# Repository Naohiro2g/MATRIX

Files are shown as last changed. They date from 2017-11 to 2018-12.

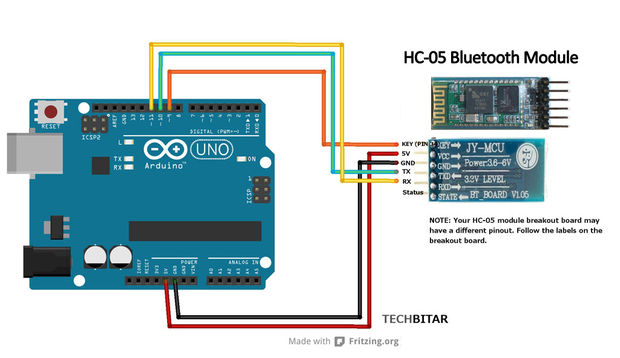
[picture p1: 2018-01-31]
Test/Setup/HC05_BT_config/HC05_BT_config_connect.jpg

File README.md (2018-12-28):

# Otto LED Matrix for mouth emotions

LED mouth Matrix use the [MAX7219](https://es.aliexpress.com/item/1pcs-MAX7219-dot-matrix-module-microcontroller-module-display-module-finished-goods/32725083862.html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)
+Touch sensor use this [2PCS TTP223 Capacitive Touch Switch Button Self-Lock Module for Arduino](http://www.ebay.com/itm/2PCS-TTP223-Capacitive-Touch-Switch-Button-Self-Lock-Module-for-Arduino/131662428748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)

Here are libraries and sketches for Otto DIY robot, with all files neccesary for LED Matrix and some features under developmnet

- Bluetooth
- rechargable lipo battery
- touch sensors
- RGB led nose
- LED matrix for mouths
- internal voltage measurment

v2 sketch is for version with 2 buttons for mode change (first button dance, second button walk+avoid, both together = react to noise)
v3 sketch has only 1 button or touch sensor and changes modes on touch (dance -> walk -> react to noise -> standby -> dance....)
Everything else is the same.

## 1. Interact with other Otto builders
Join the [Otto builders group in facebook](https://www.facebook.com/groups/ottodiy/)

## 2. Buy to build or make your own Otto!
Difficult to find all the parts? then buy quality kits [from our website only](ottodiy.com), is a way to contribute and support this project to continue growing, so we can continue offering very affordable kits and constantly creating new robots open for all.
After you have all components just follow the instruction manual in the files and build your own Otto in one hour!

If you want make Otto by yourself ;) that is great too! but do not forget to add your [marker in our google map!](https://drive.google.com/open?id=1qXEfuS5egbF14gi8EUjJ6U-dITHoJJNZ&usp=sharing)

## 3. Share your innovative creation with #OttoDIY
A redesign, modified code or if your creation is different but inspired in Otto; is technically a remix, so please share in our [Wikifactory Social & Design Platform](https://wikifactory.com/+OttoDIY) or please post that you have [made/remix an Otto in Thingiverse and add to this group] (https://www.thingiverse.com/groups/ottodiy) or pull a request here in Github!

Keep sharing with us in any social media, tag friends, family with #OttoDIY and make sure more robot fans do the same everywhere, we love to see Otto robots around the world!

Please help us to spread out the word first in Maker Faires, Maker spaces, Hacker spaces, Schools, Universities, tech events and so on...

## 4. Otto DIY robot for STEAM education 
Educational deep content for STEAM centers, we already partner with many tech companies, entrepreneurs, educational centers and schools around the world, just contact us to be an official collaborator, we easily adapt to different curriculum or needs and we can leverage your ideas too!
Add your [organization in our google map](https://drive.google.com/open?id=1qXEfuS5egbF14gi8EUjJ6U-dITHoJJNZ&usp=sharing) and do not hesitate to contact us

Stay active in our social media for contest and awards to the best Otto builders and as always so we will keep sharing this knowledge to the world and the humanity.

Truly opensource hardware!

## License CC-BY-SA
<br /><span xmlns:dct="http://purl.org/dc/terms/" property="dct:title">Otto DIY</span> by <a xmlns:cc="http://creativecommons.org/ns#"  property="cc:attributionName"> [www.ottodiy.com](http://www.ottodiy.com) </a> is licensed under a <a rel="license" href="http://creativecommons.org/licenses/by-sa/4.0/">Creative Commons Attribution-ShareAlike 4.0 International License</a>.

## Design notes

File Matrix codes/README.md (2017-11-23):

# LED Matrix (optional)

This Repository have all open source files for @jarsoftelectrical version of the popular Otto DIY 
The Arduino code is modified from the Zowi robot, it has modified to wotk with a MAX 7219 LED MATRIX as as mouth as well as other adjustments.

Please copy all the files in the OTTO_Library folder to the Arduino IDE Library folder
The code is based on the Zowi code, modified for OTTO
Please NOTE: i have moved the BUZZER to pin D13............
Please NOTE: you need pull-down resistors on the button pins............
Please NOTE: you will need a link between A7 and +5 volt to fool low battery warnings

OTTO main program is  inside the OTTO_LEDMATRIX folder, ensure you are using the latest version of the Arduino IDE.
The modifed ZOWI main program is inside the ZOWI_BASE_v2_MATRIX folder, ensure you are using the latest version of the Arduino IDE.

Happy roboting....

Otto was inspired by another robot BoB the BiPed and programmed using code from [another open source biped robot Zowi](https://github.com/bqlabs/zowi)

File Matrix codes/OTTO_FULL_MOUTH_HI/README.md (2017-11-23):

# Otto DIY PLUS

This Repository have all open source files for my version of the popular Otto DIY PLUS with the OTTO welcome on 7219MAX MATRIX LED mouth
The Arduino code is modified from the Zowi robot and original OTTO code, it has modified to work with a MAX 7219 LED MATRIX as as mouth as well as other software adjustments.

Please copy all the files in the Library folder to the Arduino IDE Library folder

The main program is inside the OTTO_FULL_MOUTH_HI folder, ensure you are using the latest version of the Arduino IDE.

Happy roboting....

Otto was inspired by another robot BoB the BiPed and programmed using code from [another open source biped robot Zowi](https://github.com/bqlabs/zowi)

## License CC-BY-SA
<br /><span xmlns:dct="http://purl.org/dc/terms/" property="dct:title">OttoDIY</span> by <a xmlns:cc="http://creativecommons.org/ns#" href="ottobot.org" property="cc:attributionName" rel="cc:attributionURL">ottobot.org</a> is licensed under a <a rel="license" href="http://creativecommons.org/licenses/by-sa/4.0/">Creative Commons Attribution-ShareAlike 4.0 International License</a>.

Otto's differences are in the assembled size (11cm x 7cm x12cm), cleaner integration of components and expressions. 
Using off the shelf and 3D printed parts, simple electronics connections (almost no welding required), and basic coding skills, [you will be able to build your own cute Otto friend in as little as two hours!](http://www.instructables.com/id/Otto-Build-You-Own-Robot-in-Two-Hours/)

### Otto is design using Autodesk 123D Design software 
[You can modify it for customization](http://www.123dapp.com/Project/Otto-build-your-own-robot/5658683) or further improvements!
Gather all the off the shelf parts in the [BOM file] (https://github.com/OttoDIY/Otto/blob/master/OTTO_V02_BOM_STP_STL/OTTO_BOM.xlsx) that you'll need for this assembly, then follow [the instruction manual] (https://github.com/OttoDIY/Otto/blob/master/OTTO_V02_BOM_STP_STL/OTTO_InstructionManual_V02.pdf)

This robot is licensed under a Creative Commons Attribution-ShareAlike 4.0 International License. Please read the LICENSE files for more details.

More info in http://ottobot.org

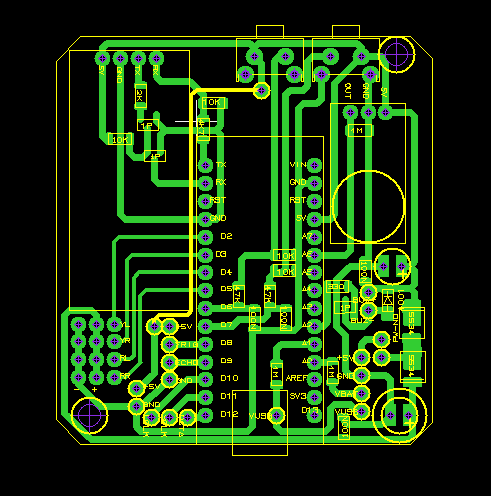
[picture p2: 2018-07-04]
PedroBot_Main_Prog/Implantation Main Board.PNG

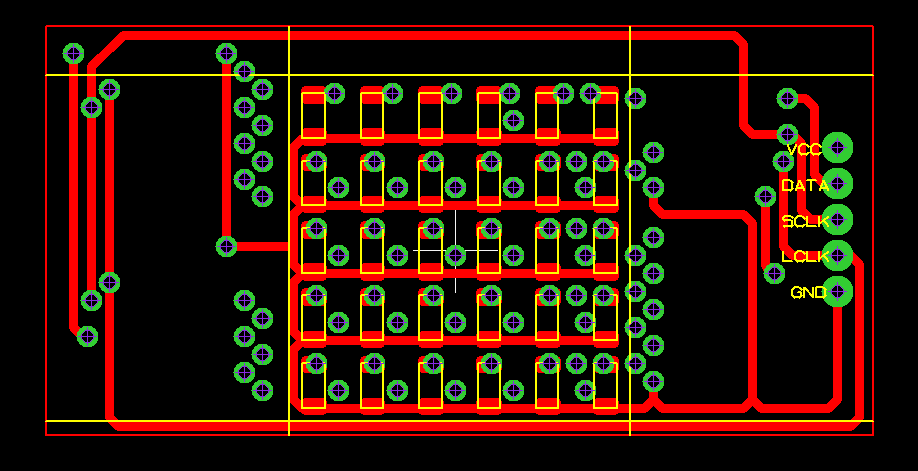
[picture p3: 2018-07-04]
PedroBot_Main_Prog/Matrix led back layer.PNG

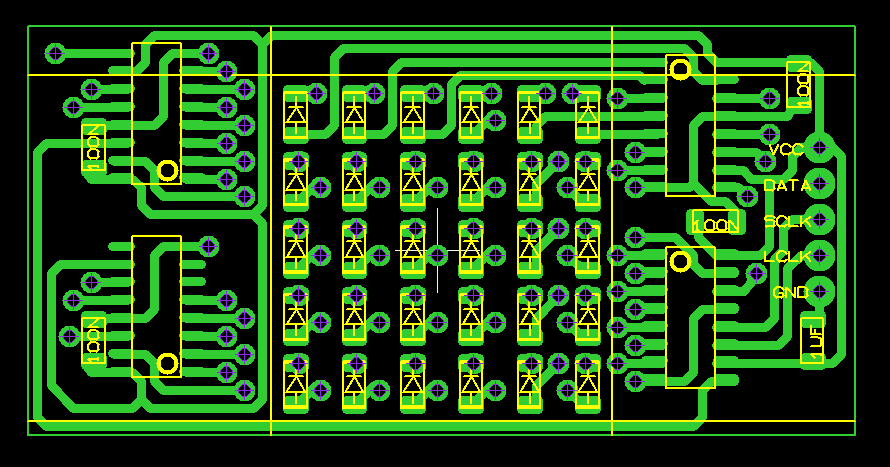
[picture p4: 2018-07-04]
PedroBot_Main_Prog/Matrix led front layer.PNG

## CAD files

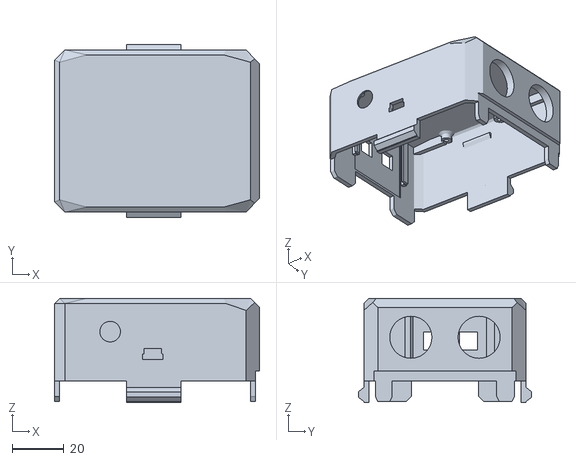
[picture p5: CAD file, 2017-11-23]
CAD/Head_MATRIX_5.stl
79.5 x 67.2 x 40.4

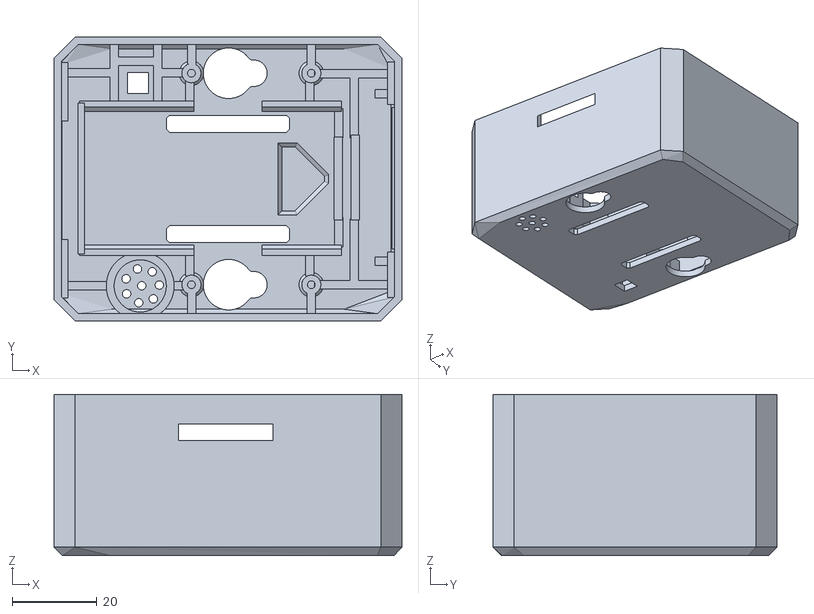
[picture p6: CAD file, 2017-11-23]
CAD/Body_MATRIX_4.stl
82.0 x 67.0 x 38.0

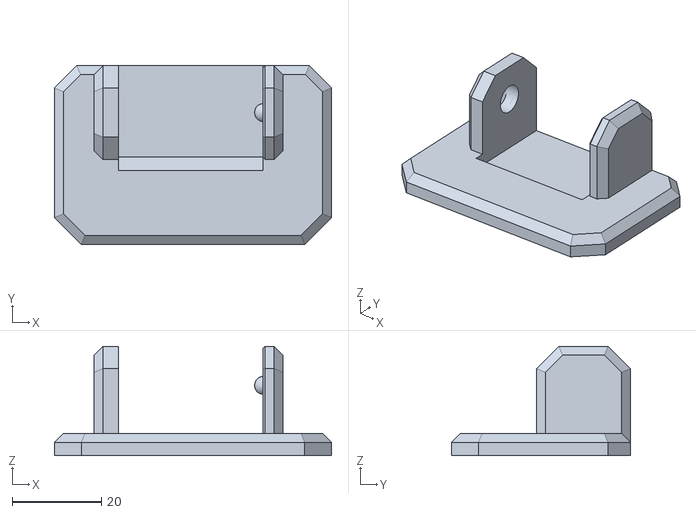
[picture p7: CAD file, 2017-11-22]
CAD/Pied droit v2.1 MG.stl
62.0 x 40.0 x 24.5

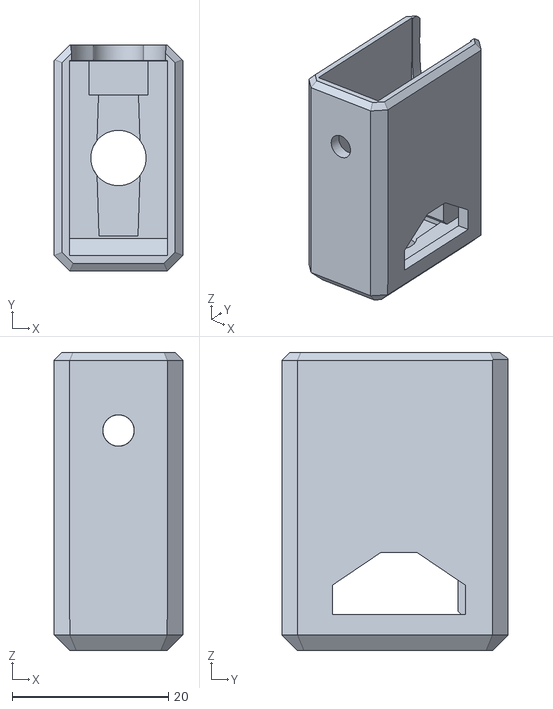
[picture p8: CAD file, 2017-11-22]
CAD/Jambes v2.0.stl
16.5 x 29.0 x 38.2

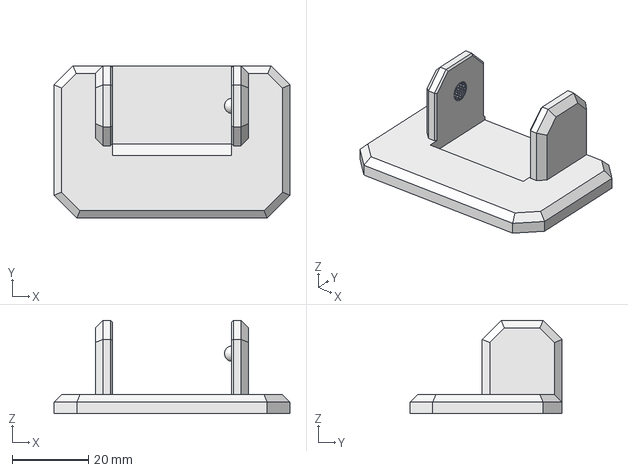
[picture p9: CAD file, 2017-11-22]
CAD/Pied droit.FCStd
62.0 x 40.0 x 24.5 mm

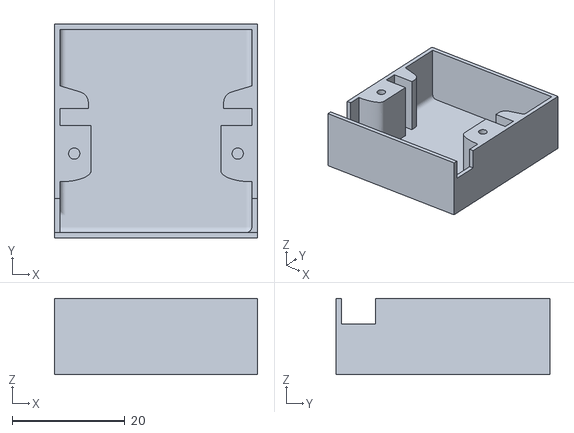
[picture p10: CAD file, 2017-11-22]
CAD/TowerPro_MG90_servo_box.STL
36.0 x 38.0 x 13.5

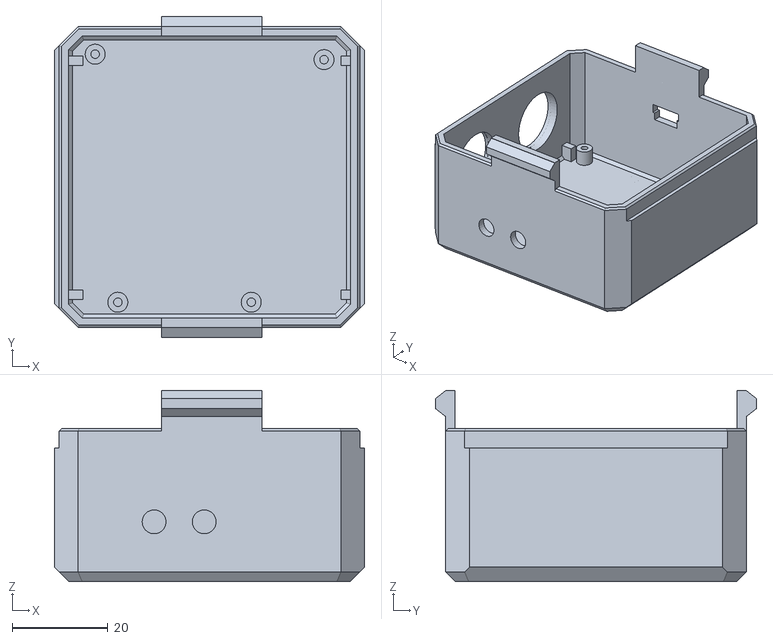
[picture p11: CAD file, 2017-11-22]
CAD/Tete v1.3.stl
65.0 x 67.2 x 40.0

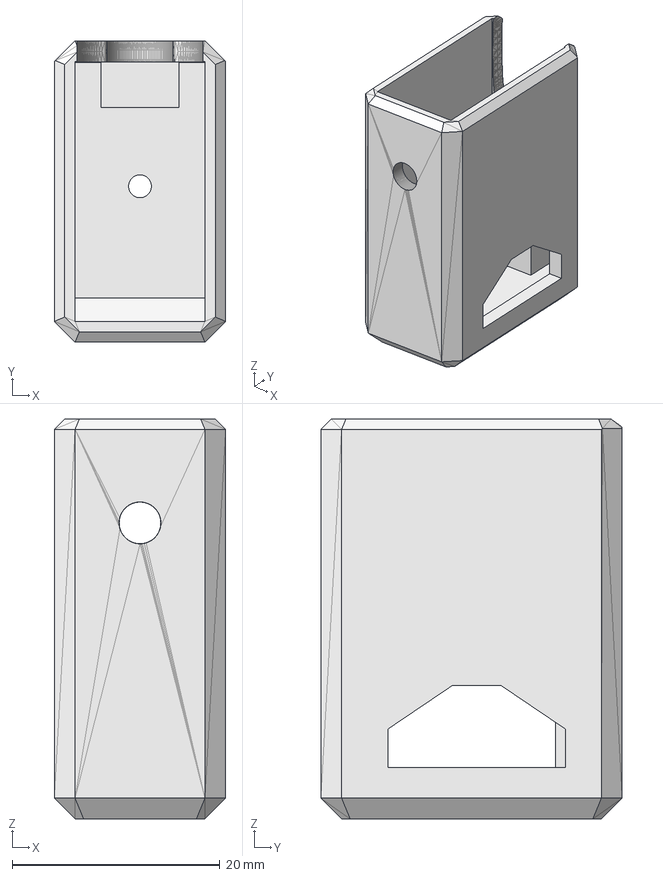
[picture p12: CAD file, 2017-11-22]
CAD/Jambes.FCStd
16.5 x 29.0 x 38.5 mm

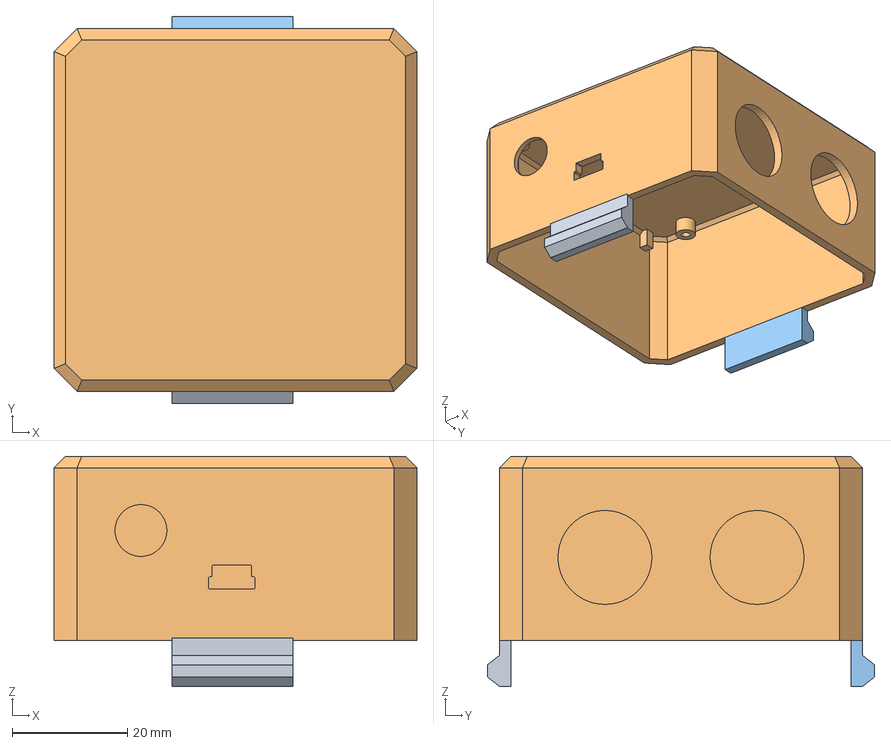
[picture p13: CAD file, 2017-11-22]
CAD/Tete.FCStd
63.0 x 67.2 x 40.0 mm
OTTO_snap037
OTTO_snap035
OTTO_snap036

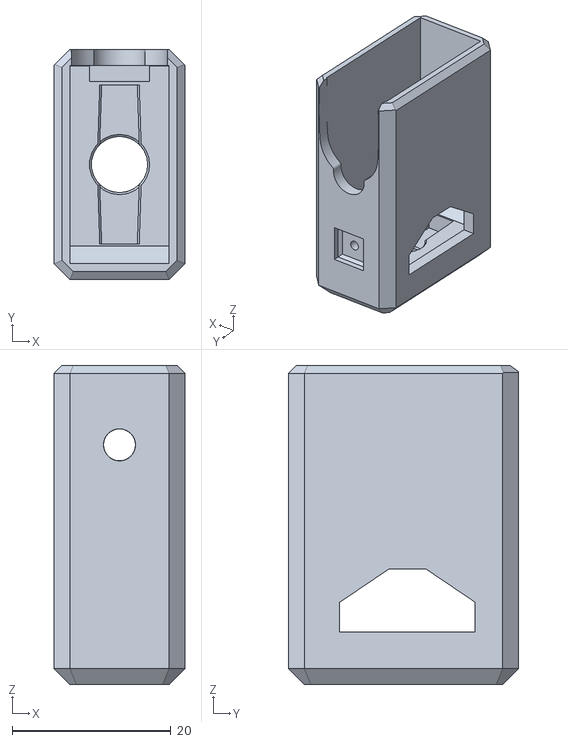
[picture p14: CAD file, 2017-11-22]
CAD/Jambes v2.2 MG.stl
16.5 x 29.0 x 40.2

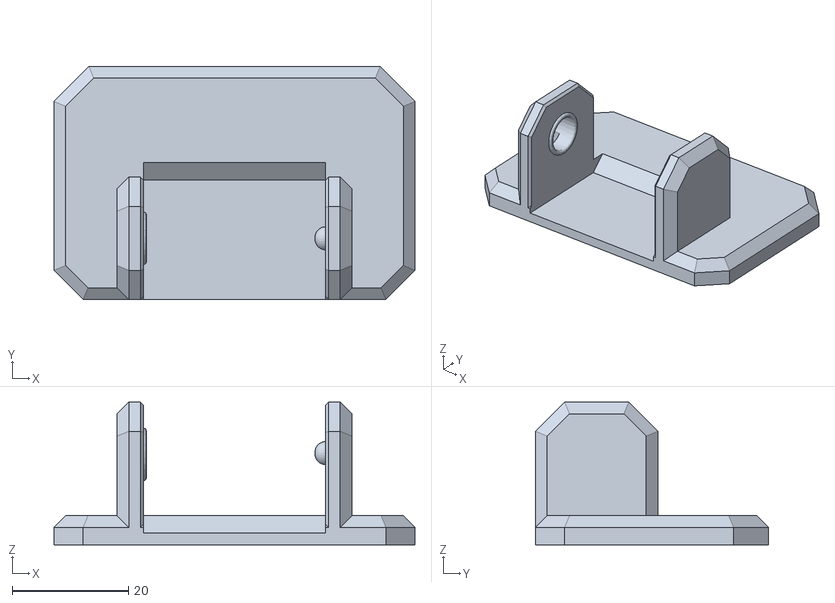
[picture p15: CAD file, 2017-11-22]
CAD/Pied gauche v2.0.stl
62.0 x 40.0 x 24.5

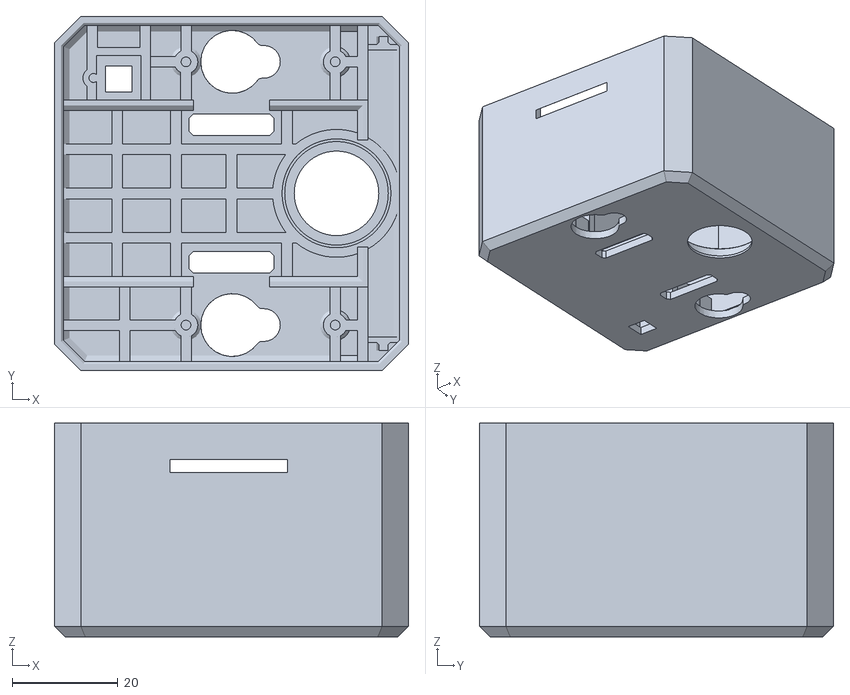
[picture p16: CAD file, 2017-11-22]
CAD/Corps v1.5 MG.stl
67.0 x 67.0 x 40.5

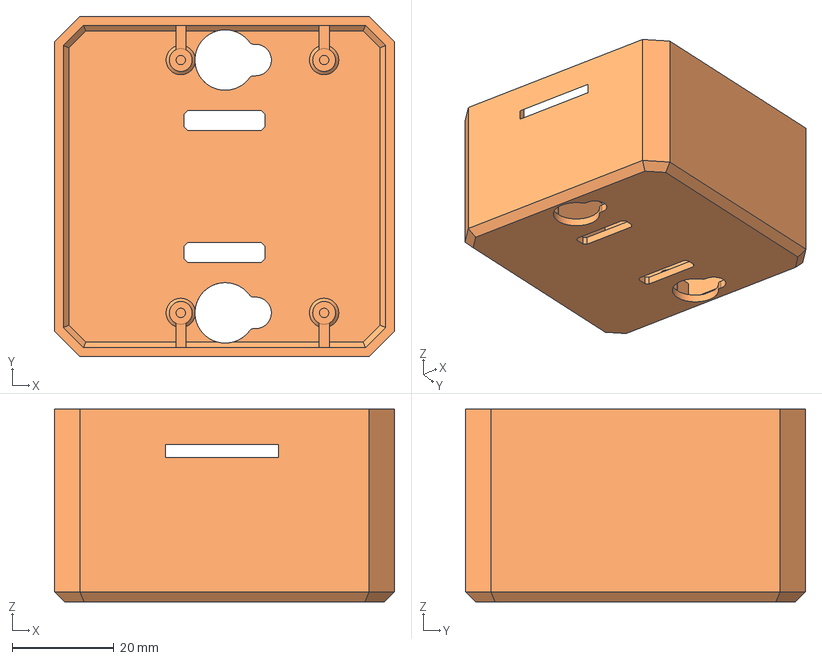
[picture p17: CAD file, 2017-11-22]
CAD/Corps.FCStd
67.0 x 67.0 x 38.0 mm

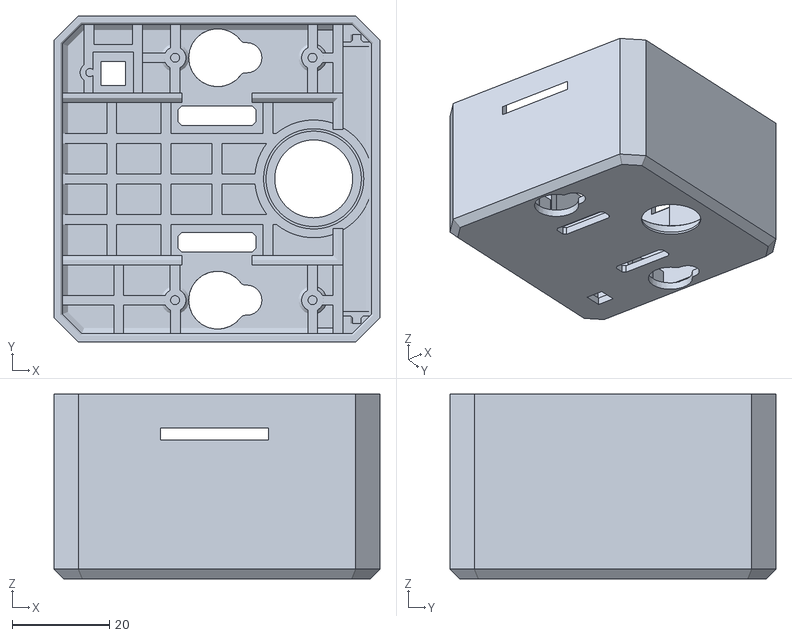
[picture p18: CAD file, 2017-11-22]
CAD/Corps v1.4.stl
67.0 x 67.0 x 38.0

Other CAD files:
CAD/Pied droit v2.0.stl
CAD/Pied gauche.FCStd
CAD/Pied gauche v2.1 MG.stl

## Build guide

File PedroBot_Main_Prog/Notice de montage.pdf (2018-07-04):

Montage de PedroBot
Auteur | Message
Pedro-51 | Sujet: Montage de PedroBot Lun 22 Mai 2017 - 1:23
| Il s'agit là d'un document que j'ai écris pour aider les enfants de mon club technologie à construire leurs robot.
| Il est bien évident que dans un cadre éducatif, il faudra fabriquer les cartes électroniques et préparer les différents éléments pour en arriver à un kit accessible aux enfants. Mais également pour celle et ceux qui souhaitent créer leurs propres robots à titre personnel, je vous invite à lire mes autres posts qui détail la marche à suivre pour fabriquer ces différents éléments.

# Montage de PedroBot

| Fabriquer un robot entièrement reprogrammable qui ce déplace tout seul, pouvant éviter des obstacles, réagir au son, danser et plus encore? Tout cela à la porté des enfants... grâce au projet PedroBot, c'est possible.
| PedroBot, qu'est ce que c'est? Il s'agit en fait de l'évolution d'un projet open source s'appelant «Otto bot» diffusé sur internet afin de faciliter l'apprentissage de la programmation aux enfants.
| Le robot que je propose et en fait une version de ma propre conception similaire à un modèle provenant d'une société Espagnol appelé BQ, qui se sont eux même inspiré du projet d'origine pour développer leur propre produit vendu en France à 129,90€ sur leurs site internet.

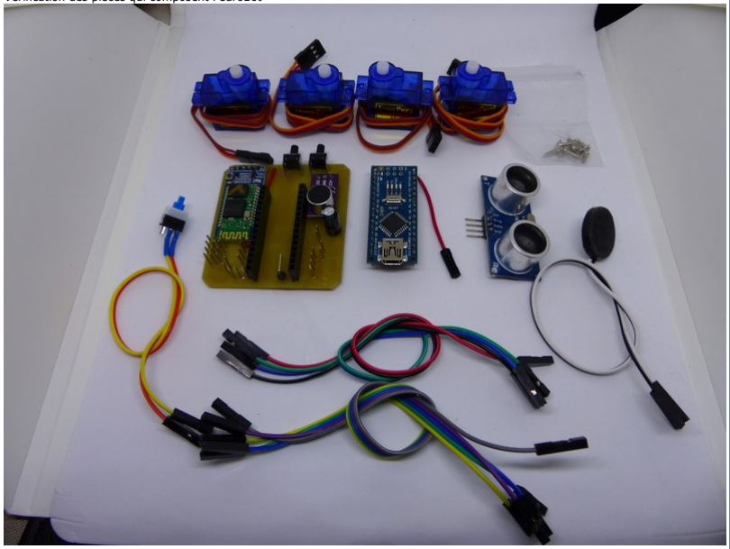
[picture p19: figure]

| Vérification des pièces qui composent PedroBot

Insére le servo-moteur dans le corps de PedroBot puis visse ce dernier.

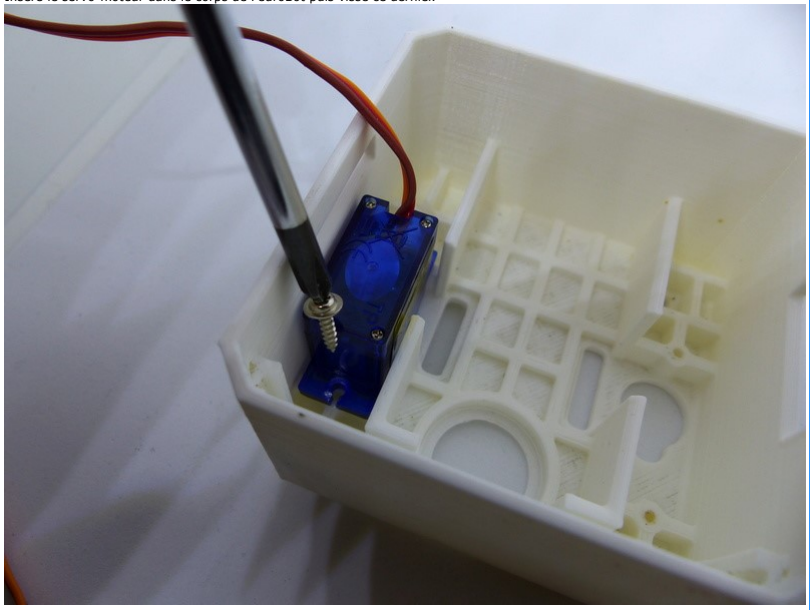
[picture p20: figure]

Fait de même pour le second servo-moteur.

Monte les jambes exactement comme sur la photo. Veille à ne pas tourner les servos-moteurs manuellement. Ils ont préalablement été réglés pour faciliter le montage.

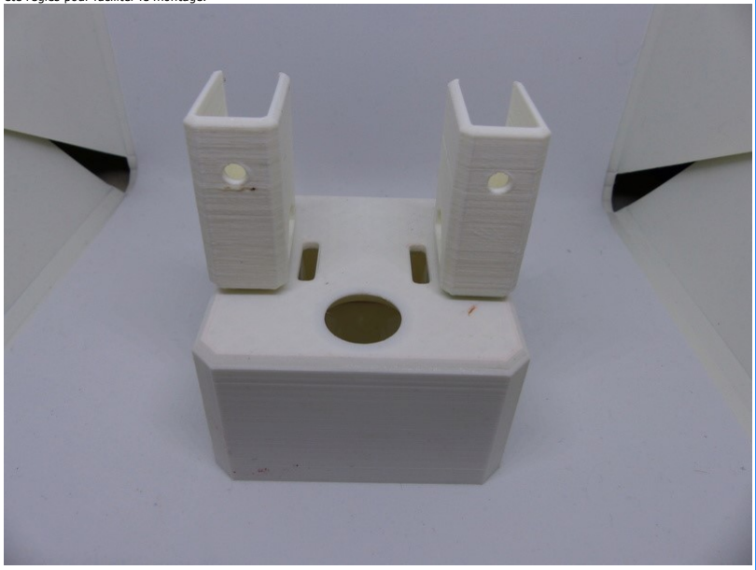
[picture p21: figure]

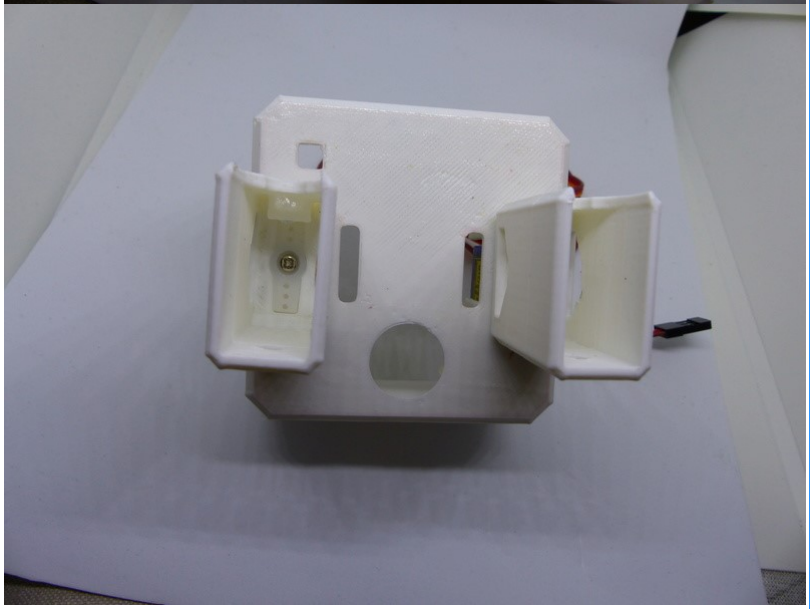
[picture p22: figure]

Insére les servos-moteurs. Comme pour les jambes, ne tourne pas les servos-moteurs manuellement.

Visse les servos-moteurs

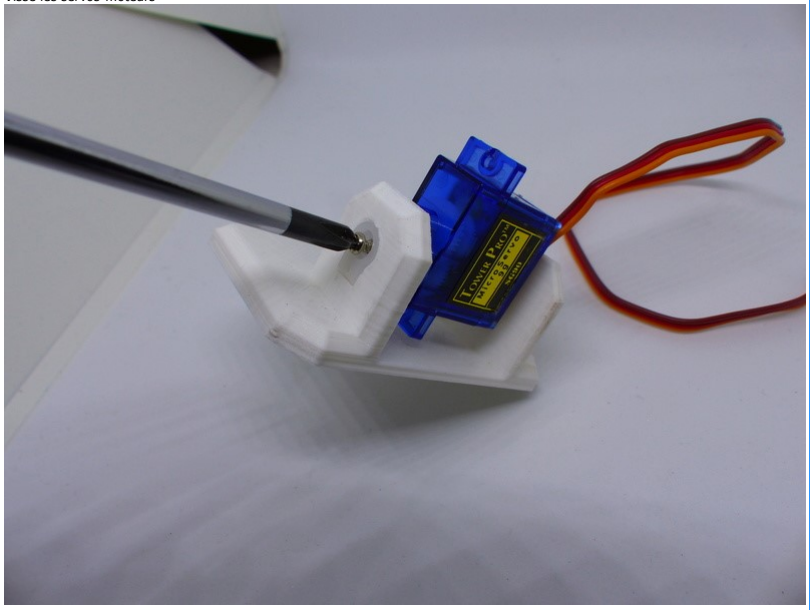
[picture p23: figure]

Place les câbles des pieds comme indiqué sur la photo.

Insére les servos-moteurs dans les jambes.

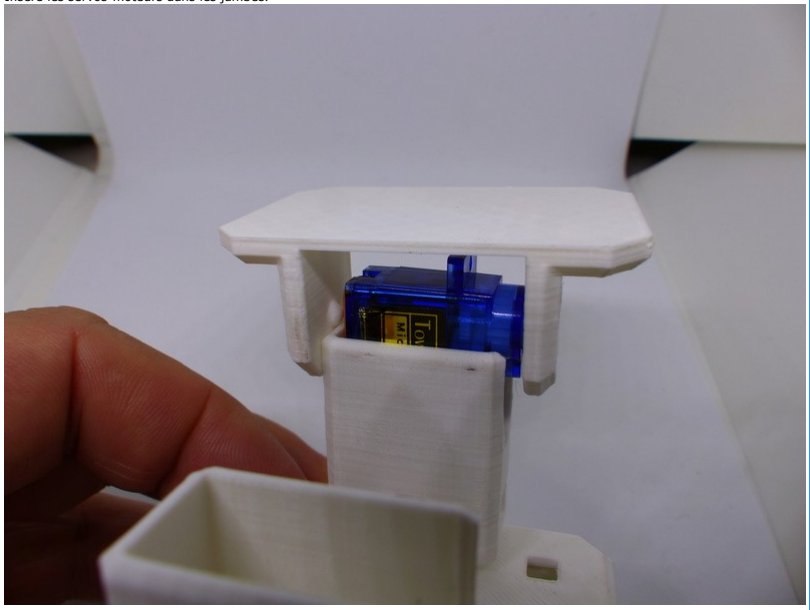
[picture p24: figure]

Visse les servos-moteurs.

Place le Haut parleur dans le corps du robot

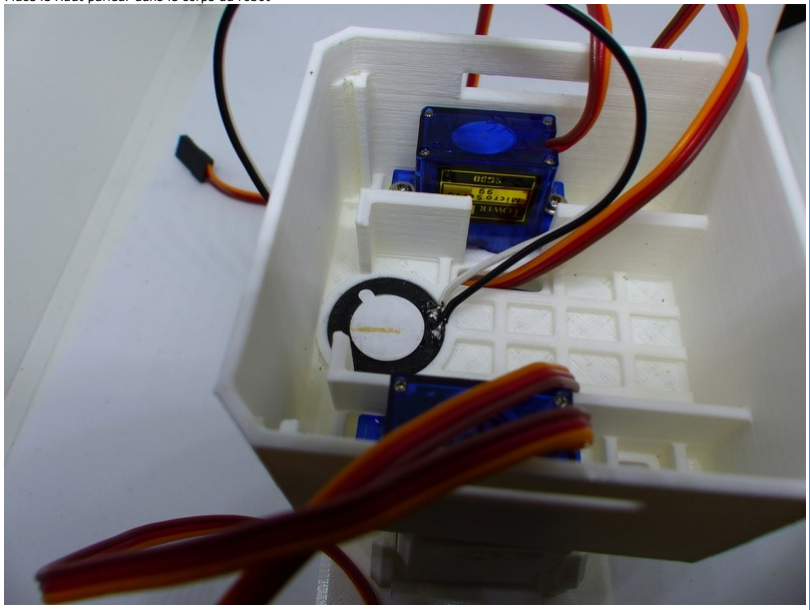
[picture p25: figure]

Fait de même pour l'interrupteur, bloque celui ci à l'aide d'une longue vis.

Prend la carte Arduino Nano et branche le câble qui permettra la charge de la batterie.

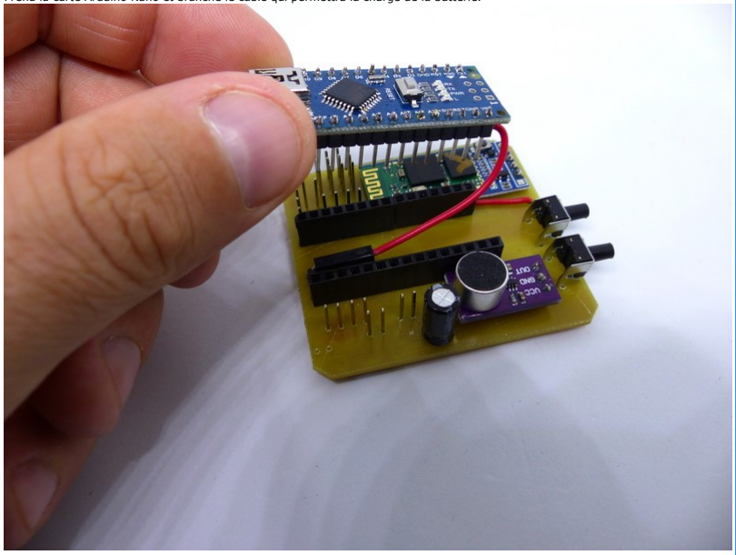
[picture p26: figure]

Insére la carte Arduino à la carte principale.

Branche les fils qui serviront à connecter le Capteur Ultrason.

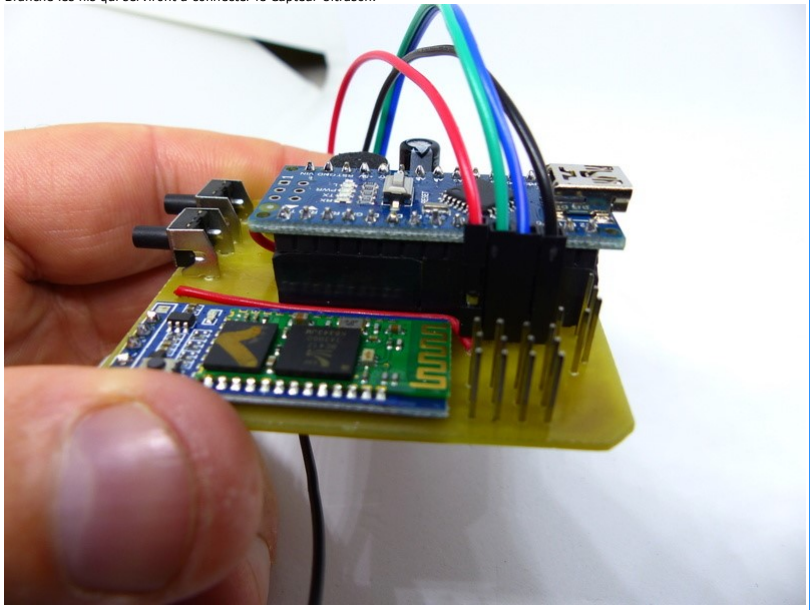
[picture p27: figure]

Branche les câbles du haut parleur et de l’interrupteur. Respecte le code couleur.

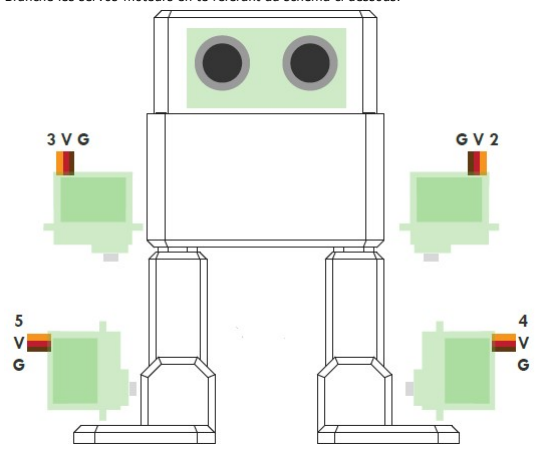
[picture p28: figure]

Branche les servos-moteurs en te référant au schéma ci dessous.

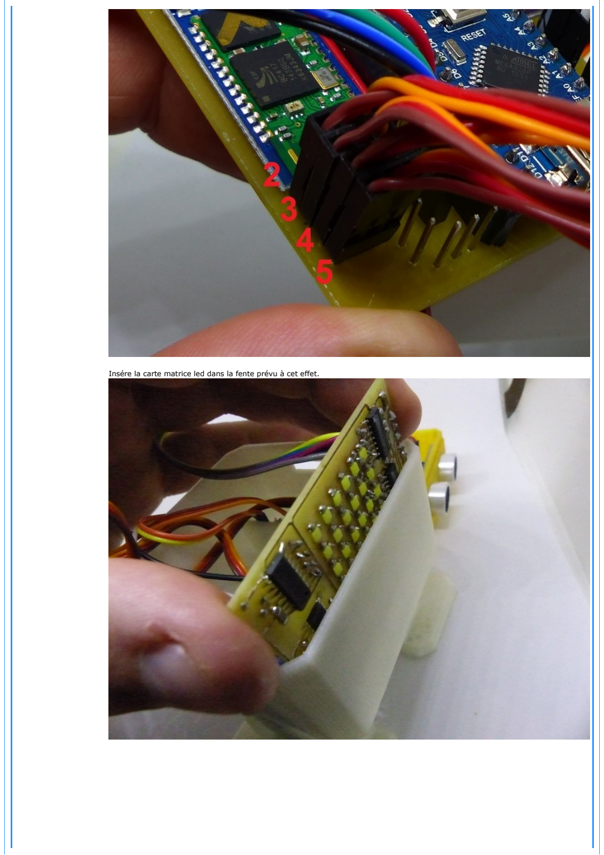
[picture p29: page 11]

Insére la carte matrice led dans la fente prévu à cet effet.

Branche la carte matrice led.

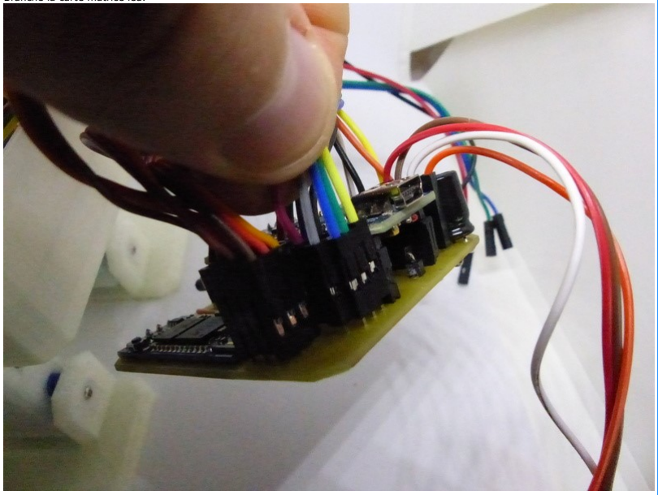
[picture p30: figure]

Branche le pack batterie

Insére le Pack batterie dans sont logement.

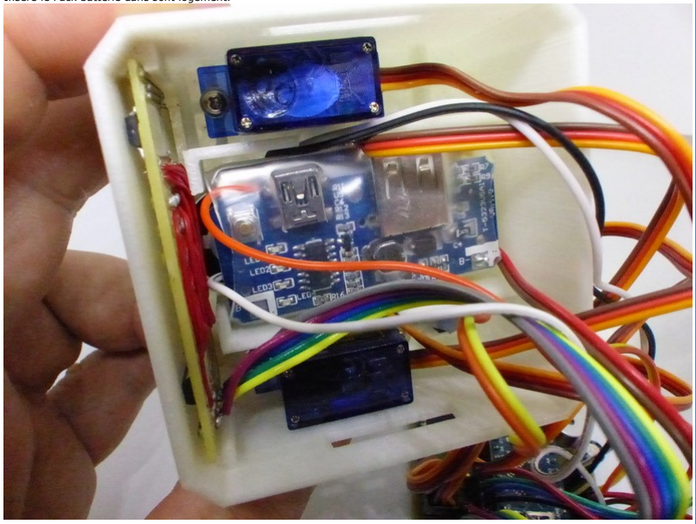
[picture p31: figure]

Insére le capteur à Ultra Son dans la tête de PedroBot.

Rentre la carte principal en diagonale en veillant a ce que les interrupteurs soit placés correctement dans leurs logements.

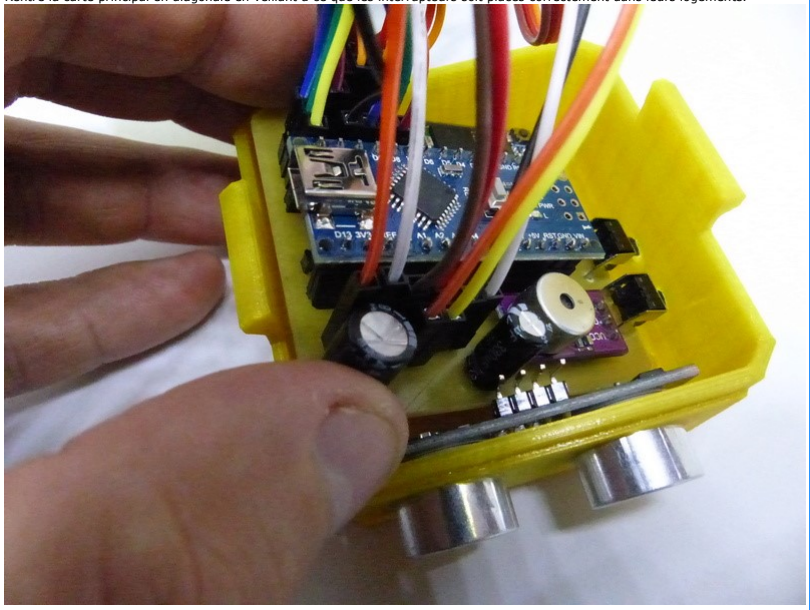
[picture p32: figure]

Enfonce la carte au fond de la tête, un clic se fera entendre lorsque le port USB sera correctement placé.

Branche les câbles du capteur Ultra Son comme suit.

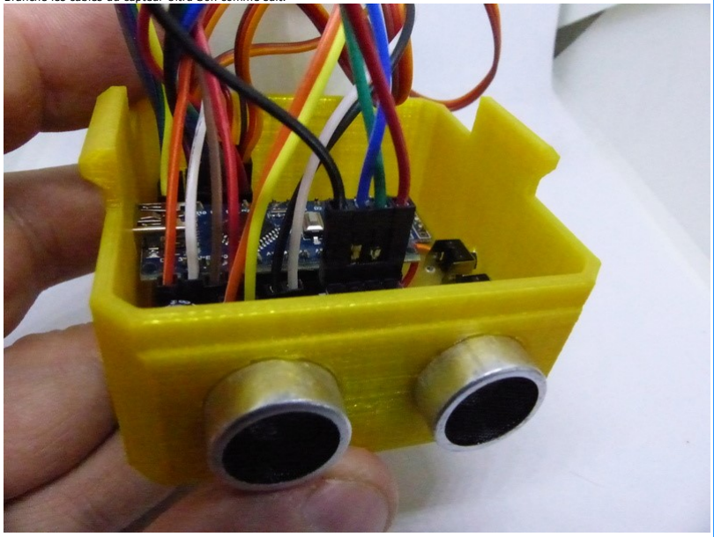
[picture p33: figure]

Branche PedroBot au pc avec un câble Usb. Ton robot va s’allumer tout seul. Le devant de la bouche risque de faire des formes aléatoires, c'est parce qu'il n'est pas encore programmé.

Programmation de PedroBot.
Installation de Arduino. Il s'agit du logiciel qui permettra de programmer ton robot. Pas d’inquiétude, Tu n'a pas besoin d'avoir des connaissances avancés en programmation, si tu suit à la lettre les instructions qui vont suivre, tu va t'en sortir comme un chef. Avec l'accord de tes parents, il te faut tout d'abord télécharger l'IDE Arduino sur le site officiel et l'installer. Le logiciel ce trouve à la page suivante: https://www.arduino.cc/en/Main/Software Procède à l'installation du logiciel Arduino.
Tu aura aussi besoin du programme pour ton robot. J'ai créer pour cela un dossier avec tout les fichiers nécessaires pour la programmation et l'utilisation de PedroBot. Il est téléchargeable à cette adresse: PedroBot User Conserve ce dossier précieusement sur ton PC, il te servira plus tard pour jouer avec ton robot.
Dans un premier temps, une fois le fichier "PedroBot User" téléchargé et dézippé, il faudra copier le dossier "Arduino" sur ton ordinateur a cet emplacement "Ce PC\Documents". Ce sont des fichiers essentiels qui permettrons de programmer correctement ton robot.
Dans le dossier "PedroBot_Main_Prog", Lance le fichier du même nom.
Cela à pour effet de lancer le logiciel Arduino avec le programme principal du robot.
Dans le Menu "Outils\Type de carte" choisit "Arduino Nano".

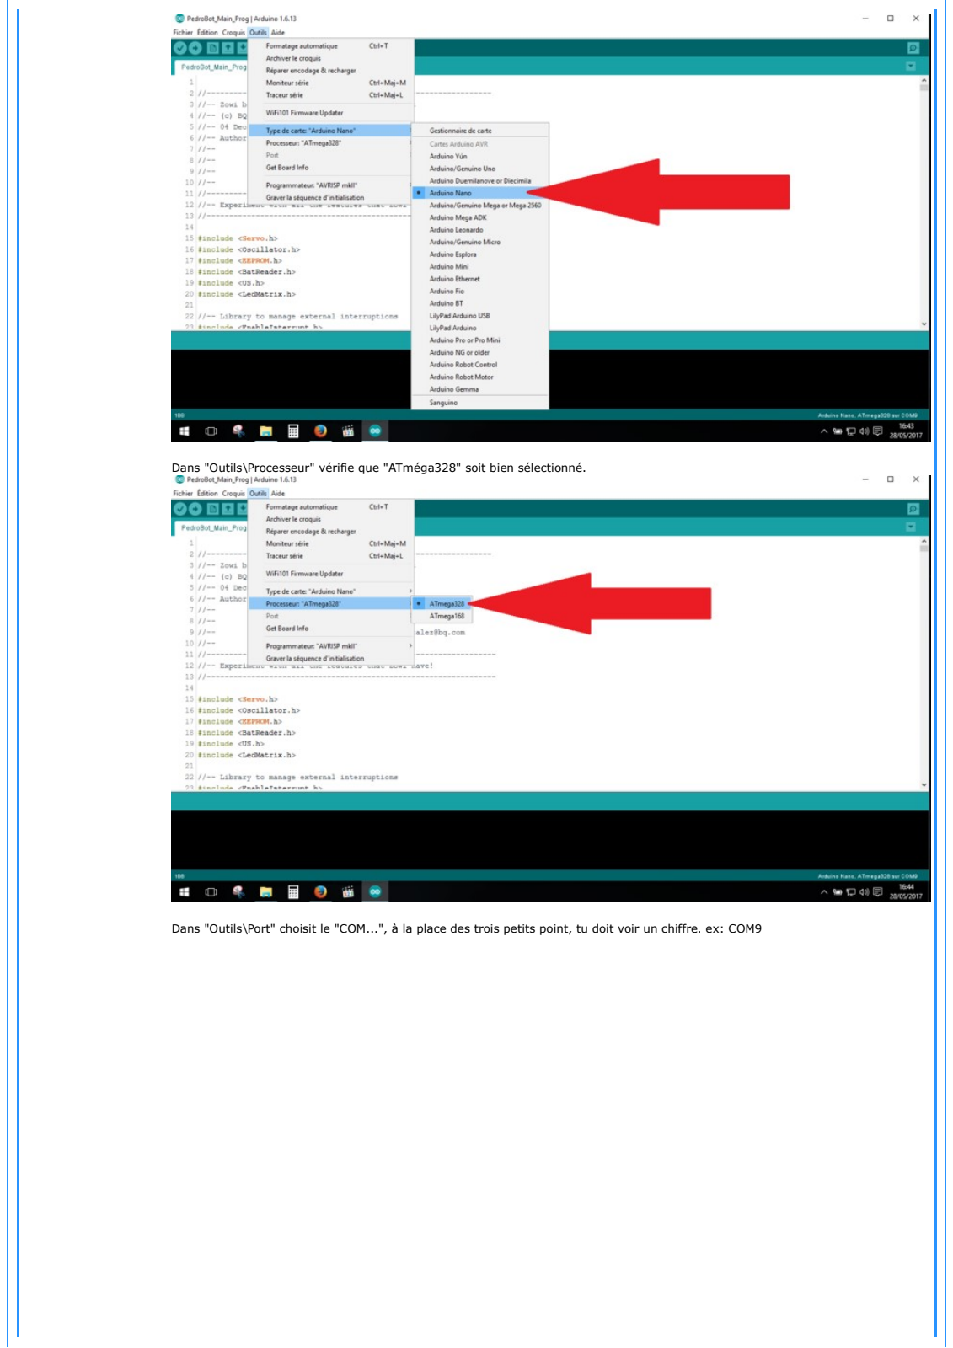
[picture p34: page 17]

Dans "Outils\Processeur" vérifie que "ATméga328" soit bien sélectionné.

Dans "Outils\Port" choisit le "COM...", à la place des trois petits point, tu doit voir un chiffre. ex: COM9

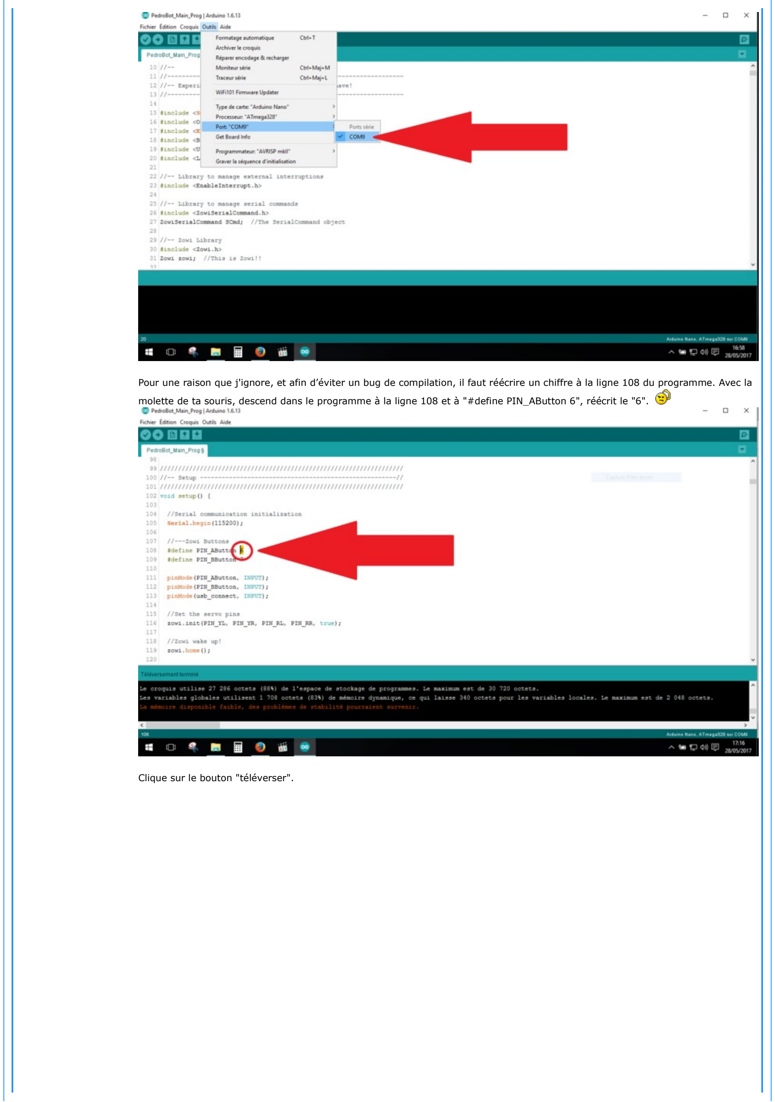
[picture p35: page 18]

Pour une raison que j'ignore, et afin d’éviter un bug de compilation, il faut réécrire un chiffre à la ligne 108 du programme. Avec la molette de ta souris, descend dans le programme à la ligne 108 et à "#define PIN_AButton 6", réécrit le "6".

Clique sur le bouton "téléverser".

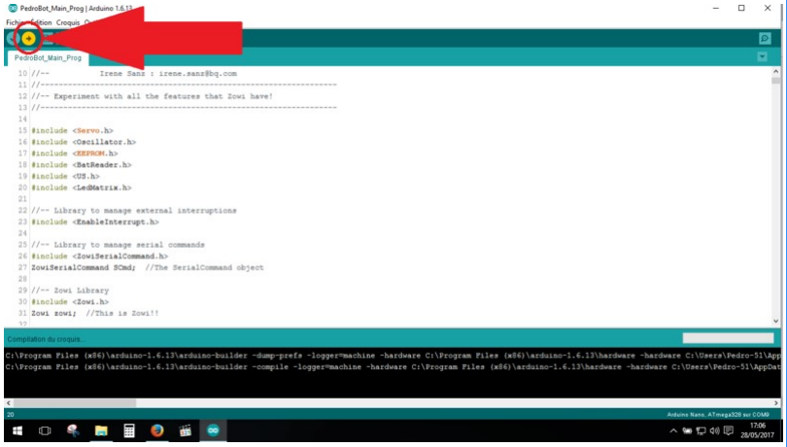
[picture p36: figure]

Tu devrait obtenir un message comme quoi tout c'est bien déroulé.

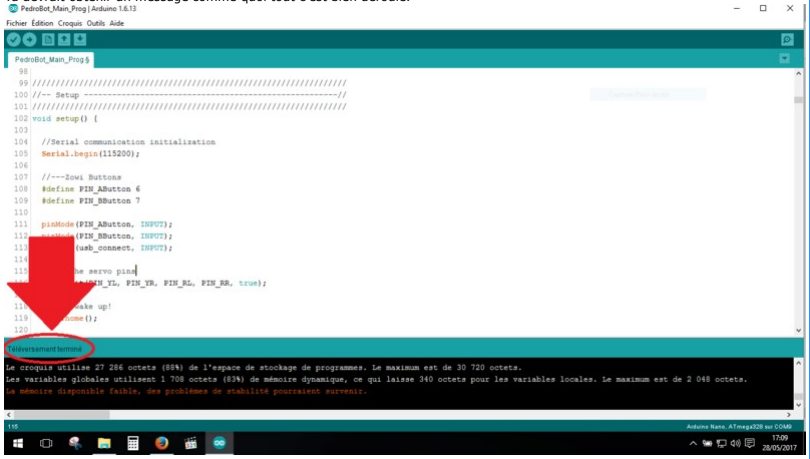
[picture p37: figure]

Mode d'emploi de PedroBot PedroBot à trois mode principaux.Je décrit ici comment les activer mais également leurs fonctionnements. - Mode Danse

Pour activer ce mode, appuye sur le bouton A. PedroBot valide et affiche le chiffre 1. Dans ce mode, le robot fait des pas de danses et change d'expressions de manière totalement aléatoire. C'est carrément plus drôle avec un fond musical bien sûr. - Mode déplacement

Pour activer ce mode, appuye sur le bouton B. PedroBot affiche le chiffre 2. Dans ce mode, le robot ce déplace en avant et s'il détecte un obstacle, change de direction. - Mode surveillance

Pour activer ce mode, appuie sur les boutons A et B en même temps. PedroBot affiche le chiffre 3. Dans ce mode, PedroBot va se mettre en attente et si tu lui tape sur la tête, il réagira en émettant un son de mécontentement et fera un mouvement aléatoire.
L'application pour commander PedroBot.
Mais c'est pas tout, PedroBot à aussi une fonction Bluetooth. Il faudra télécharger l'application "Zowi App" sur ton téléphone Android afin de profiter de toutes les fonctions de PedroBot.

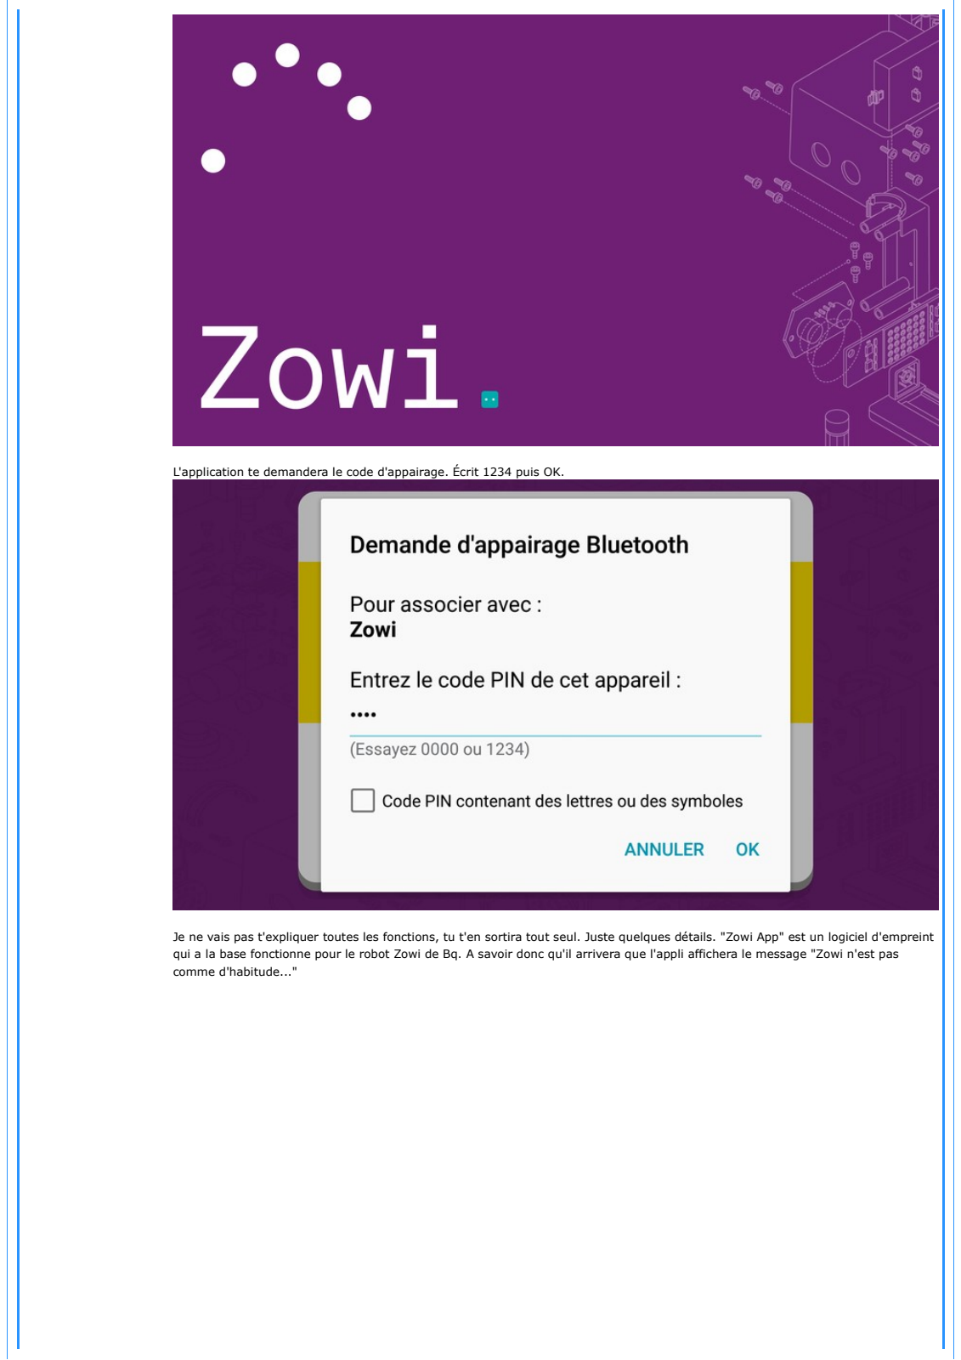
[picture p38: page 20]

L'application te demandera le code d'appairage. Écrit 1234 puis OK.

Je ne vais pas t'expliquer toutes les fonctions, tu t'en sortira tout seul. Juste quelques détails. "Zowi App" est un logiciel d'empreint qui a la base fonctionne pour le robot Zowi de Bq. A savoir donc qu'il arrivera que l'appli affichera le message "Zowi n'est pas comme d'habitude..."

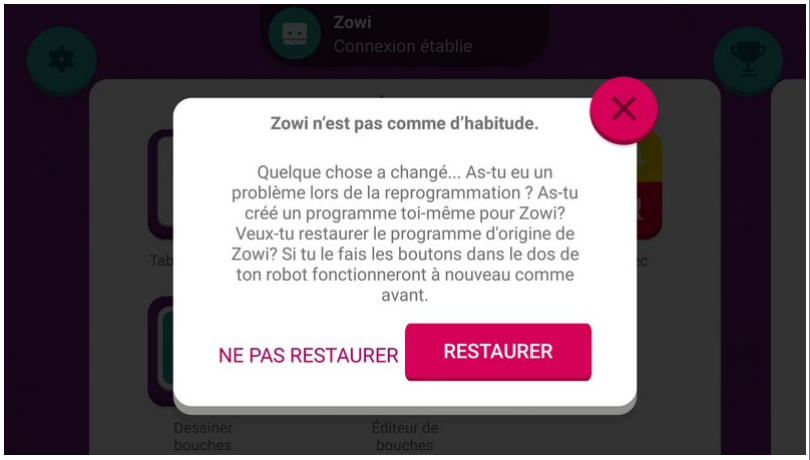
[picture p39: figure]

Il faudra simplement cliquer sur "Ne pas restaurer". Pas de panique, si tu appuie sur "Restaurer", cela ne fonctionnera pas tout simplement, tu aura seulement perdu du temps.
Dans la partie droite de l'application, il y a des petits jeux de découverte. Si le téléphone n'est pas connecté à internet, j'ai pensé à te faciliter la tache en sauvegardant les dites pages de présentation dans le dossier "Pages site Bq". Il suffira alors d'ouvrir la page correspondant au jeux que tu aura choisi au lieu de cliquer sur "Afficher le projet."

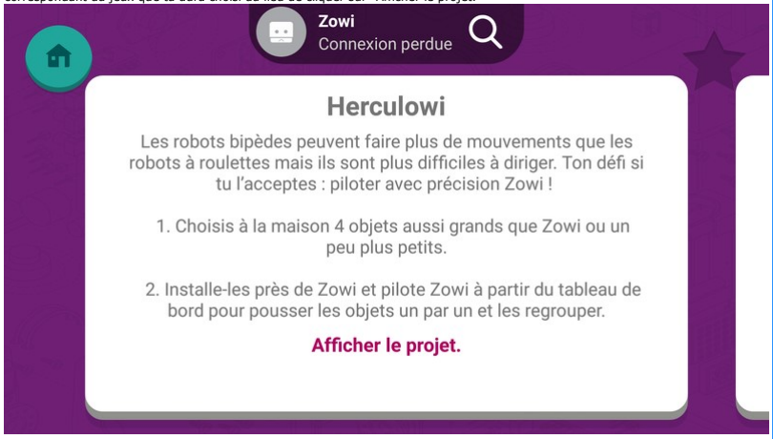
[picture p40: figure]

Pour "Super Zowi" et "Devinowi, il ne sera pas possible de reprogrammer directement via l'application de ton téléphone. Mais de la même manière qu'avec le programme principal, tu pourra reprogrammer PedroBot pour lui apprendre de nouvelle fonctions.

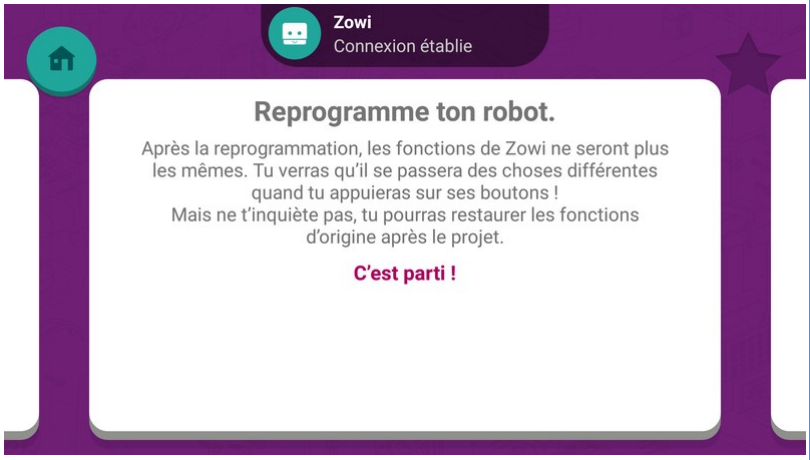
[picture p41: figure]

Il suffira d'aller dans le dossier "PedroBot User\Jeux Zowi", de choisir le programme du jeu que tu souhaite, de cliquer dessus pour démarrer le logiciel Arduino et suivre la procédure de programmation du robot décrite précédemment.
Par ailleurs, tu ne pourra pas utiliser Bitbloq dans les jeux associés, mais tu pourra toujours essayer de répondre aux questions pour débloquer les boutons sous cadenas de l'application.
Voila, tout est dit... Et maintenant amuse toi bien avec ton robot.

## Montage de PedroBot

Panneau d'administration
Forum gratuit | phpBB | Forum gratuit d'entraide | Statistiques | Contact | Signaler un abus

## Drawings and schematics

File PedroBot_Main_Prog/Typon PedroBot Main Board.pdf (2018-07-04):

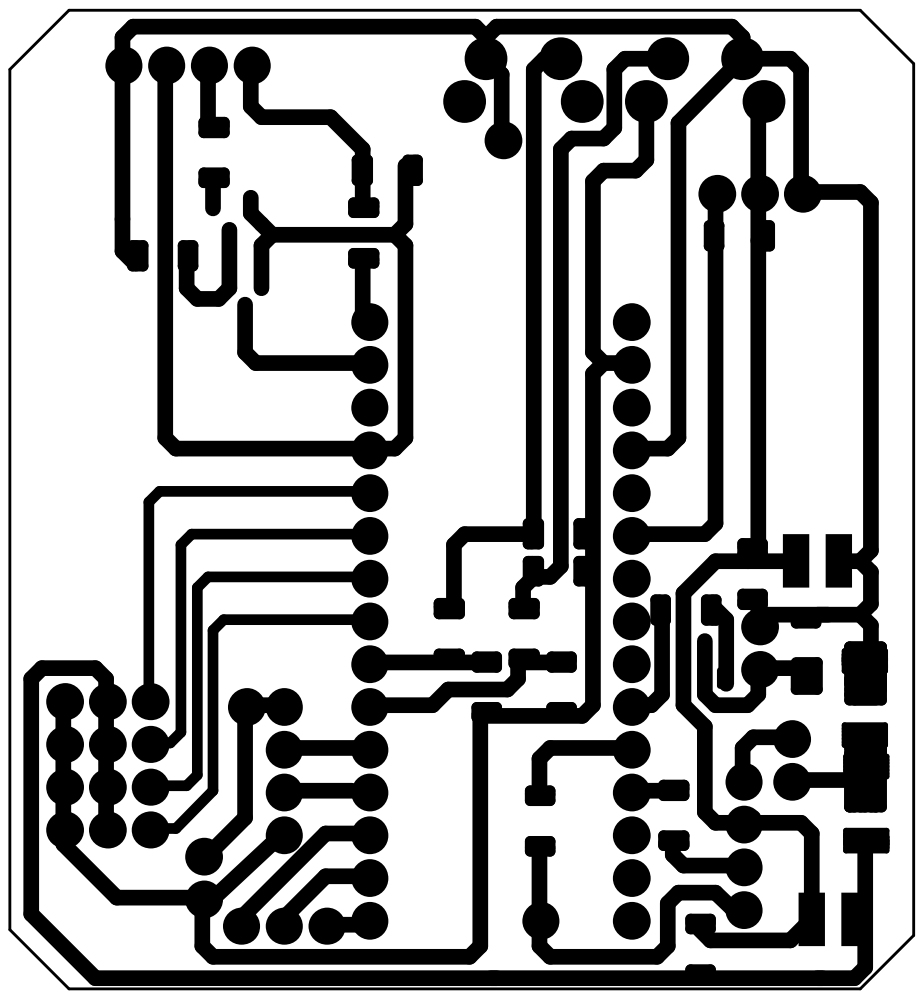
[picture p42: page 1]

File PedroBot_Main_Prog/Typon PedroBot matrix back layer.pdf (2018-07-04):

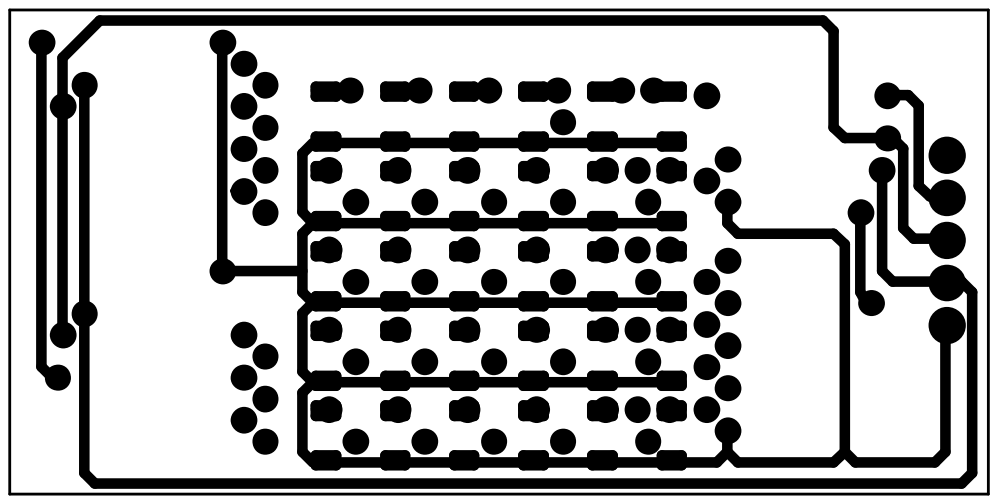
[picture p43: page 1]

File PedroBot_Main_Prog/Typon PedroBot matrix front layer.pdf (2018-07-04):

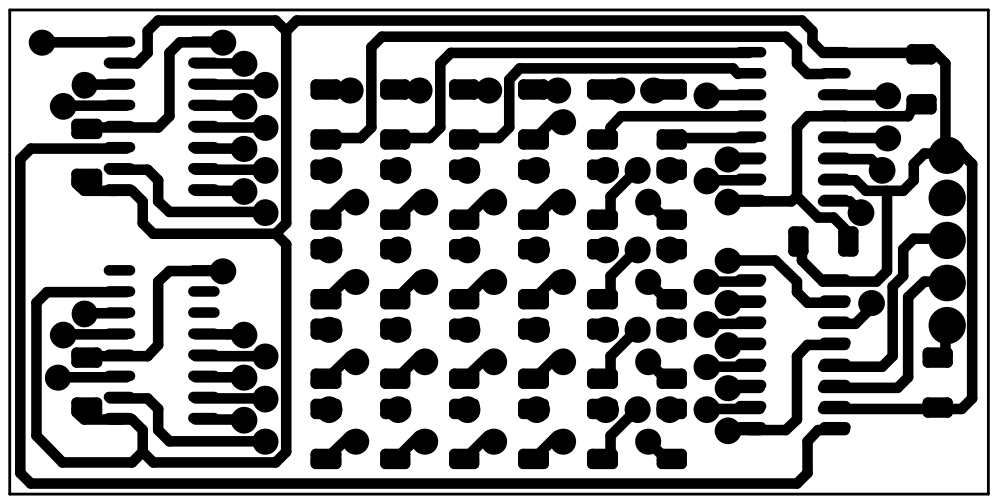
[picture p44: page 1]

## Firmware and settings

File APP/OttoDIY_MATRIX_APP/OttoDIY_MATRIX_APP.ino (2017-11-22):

#include <Servo.h>

/* Programa Otto v 1.1.0 by Fernandezaginer
 * Abril 2017 (1.1.0 en Mayo 2017)
 * Programa creado originalmente por Andrés Fernández Muñoz  */


/////////////////////////////////////////////////////////////////
/////////////************INSTRUCTIONS************////////////////
/////////////////////////////////////////////////////////////////
 

/*                              ENGLISH
 *  
 *  1 You have to put the pins that you have puted on the Arduino
 *    in the variables called PINES. (Lines 80-110)
 *  
 *  2 You have to calibrate the Servomotors puting the angle that
 *    correspond with the angle that makes that the robot is 
 *    straight with the varaiables VCA VCB VCD and VCD, try to 
 *    change the values it must to be around 90 degrees.
 *    (Lines 130-135).
 *    
 *  3 Select your tipe of led (Negative or Positive common)
 *    in (Line 139) If it is Negative put 1 or 2 if it is 
 *    positive.
 *   
 *  4 If you have used the Chinese Arduino Nano you have to 
 *    instal the drivers.
 *  
 *  5 Select in Tools: The Plate (Arduino Nano), The ATheart 
 *    (ATmega328) and the port, if you don't know the port you 
 *    can find in the Administrator of decives in control panel
 *    an example is (COM3).
 *    
 *  6 Now we are ready to upload the progran, remember to conect
 *    the plate and clic at upload or Ctrl+U.
 *    
 *  * If you have any question ask me on
 *    http://www.thingiverse.com/thing:2083489/#comments
 *    or by email fernandezaginer@gmail.com .
 */


 /*                              ESPAÑOL
 *  
 *  1 Pon los pines que has conectado en tu arduino en la seccion
 *    de pines (Lineas 80-110)
 *  
 *  2 Calibra los servomotores en la seccion de variables valores
 *    calibrados, poniendo un valor aproximado en el que coincida
 *    cuando el robot esté recto, tendras que cargar varias veces
 *    el programa con los valores que has puesto.
 *    (Lineas 130-135)
 *    
 *  3 Selecciona el tipo de led (Negativo o Positivo común) en la
 *    (linea 139), pon 1 si es de negativo común o 2 si es de  
 *    positivo común
 *   
 *  4 Si has usado el Arduino Nano chino instala sus drivers
 *  
 *  5 Selecciona la placa en Herramientas/Placa (Arduino Nano),
 *    selecciona el procesador en Herramientas/Procesador 
 *    (ATmega328) y sececciona le puerto en Herramientas/Puerto
 *    si no saves el puerto puedes saberlo en el Panel de
 *    Control / Hardware y sonido / Administrador de 
 *    dispositivos, un ejemplo seria (COM3).
 *    
 *  6 Hahora ya podemos cargar el programa a nuestro arduino, 
 *    recuerda conectar la placa y cargalo en 'Subir' o Ctrl+U.
 *    
 *  * Si tienes alguna duda puedes preguntarmela en:
 *    http://www.thingiverse.com/thing:2083489/#comments
 *    o por un correo fernandezaginer@gmail.com .
 */


/////////////////////////////////////////////////////////////////
/////////////////////************PINES************///////////////
/////////////////////////////////////////////////////////////////
//PIN 0 BT
//PIN 1 BT

//Ultrasonidos
byte pinuttrig=3;
byte pinutecho=2;

//Servos
byte pinaservo=4;
byte pinbservo=5;
byte pincservo=6;
byte pindservo=7;

//Led RGB
byte pinLRGBr=11;
byte pinLRGBg=9;
byte pinLRGBb=10;

//Otros
byte pinbuzzer=14;
byte pinbot=13;

//Carita
byte pincaa=15;
byte pincab=16;
byte pincac=17;
byte pincad=18;

//Servos
Servo aservo;
Servo bservo;
Servo cservo;
Servo dservo;

/*   Remember the Positions of the Servos
            --------------- 
           |     O   O     |
           |---------------|
 Servo B→ |                | ← Servo D
            --------------- 
               ║     ║
               ║     ║
 Servo A→   -----   ------  ← Servo D */


////////////////////////////////////////////////////////////////
/////////************VARIABLES************//////////////////////
////////////////////////////////////////////////////////////////

// Valores Calibrados 
/*Put here the values calibrated (degrees) */
int VCA=85;
int VCB=70;
int VCC=72;
int VCD=90;

// Led RGB
/*Put here the tipe of your led*/
int Led=1;       // 1=Negativo Comun , 2=Positivo Comun


//Variables
int bt;
int conta=1;
int contb=59;

//Varialbles de movimiento
byte estado=0;
byte car=0;
byte esp=0;
byte EstabaPuntillas=0;
byte EstabaAsustado=0;
int vel=150;

//Ultrasonidos
int duracion;
int distancia;
int distanciamax=20;
boolean ut=1;

// Notas Buzzer
int nota[12] = {262,277,294,311,329,349,369,392,415,440,466,494};
/* NOTAS
 * 1=DO 2=DO# 3=RE 4=RE# 5=MI 6=FA 7=FA# 
 * 8=SOL 9=SOL# 10=LA 11=SIb 12=SI
 */

/////////////////////////////SETUP///////////////////////////////

void setup() {
  
  Serial.begin(9600);
  
  /*Inicializar Pines*/
  pinMode(pinuttrig,OUTPUT);
  pinMode(pinutecho,INPUT);
  aservo.attach(pinaservo);
  bservo.attach(pinbservo);
  cservo.attach(pincservo);
  dservo.attach(pindservo);
  aservo.write(VCA);
  bservo.write(VCB);
  cservo.write(VCC);
  dservo.write(VCD);
  delay(1000);
  pinMode(pinLRGBr,OUTPUT);
  pinMode(pinLRGBg,OUTPUT);
  pinMode(pinLRGBb,OUTPUT);
  LedOff();
  pinMode(pinbuzzer,OUTPUT);
  pinMode(pinbot,INPUT);
  pinMode(pincaa,OUTPUT);
  pinMode(pincab,OUTPUT);
  pinMode(pincac,OUTPUT);
  pinMode(pincad,OUTPUT);
  

  SonidoInicioconLed();

}

/////////////////////////////LOOP////////////////////////////////

void loop() {

  /*Leer Bluetooth*/
  ReadBT();

  /*Movimientos*/
  if(estado==0){//Parado
    if(EstabaPuntillas==1){
      Quitarpuntillas();
      EstabaPuntillas=0;
    }
    if(EstabaAsustado==1){
      Desasustar();
      EstabaAsustado=0;
    }
    Parado();
  }
  if(estado==1){//Alante
    Alante();
  }
  if(estado==2){//IzquierdaN
    Izquierdan();
  }
  if(estado==3){//Derecha L
    Derechal();
  }
  if(estado==4){//Derecha N
    Derechan();
  }
  if(estado==5){//Izquierda L
    Izquierdal();
  }
  if(estado==6){//Atras
    Atras();
  }

  /*Ultrasonidos*/
  if(ut==1){
    ReadUT();
    if(distancia<distanciamax&&esp<1){
      Parado();
      Ponerpuntillas();
      LedRosa();
      for(distancia>distanciamax;distancia<distanciamax+2||ut==0;){
        ReadUT();
        if(distancia<distanciamax+2){
          ReadUT();
          if(distancia<distanciamax+2){
            ReadUT();
            if(distancia<distanciamax+2){
              ReadUT();
              if(distancia<distanciamax+2){
                ReadUT();
              }
            }
          }
        }
        delay(300);
      }
      Quitarpuntillas();
    }
  }
  if(ut==0){
    ReadUT();
  }

  /*Funciones especiales
   *- Baile              'o' 1
   *- Asustar            'p' 2
   *- Saludo             'q' 3
   *- Puntillas          'r' 4
   */
   if(esp==1){
     Baile();
   }
   if(esp==2){
    if(EstabaAsustado==0){
      Asustar();
      delay(500);
    }
    EstabaAsustado=1;
   }
   if(esp==3){
     Saludo();
     esp=0;
   }
   if(esp==4){
    if(EstabaPuntillas==0){
      Ponerpuntillas();
    }
    EstabaPuntillas=1;
   }

  /*Caritas*/
  if(car==0){//Sonriente
    LedVerde();
  }
  if(car==1){//Sorprendida
    LedCian();
  }
  if(car==2){//Regular
    LedAmarillo();
  }
  if(car==3){//Triste
    LedRojo();
  }
  if(car==4){//Off
    //LedOff();
  }
  
  delay(10);

  
}


///////////////////////////////////////////////////////////
///////////************CONFIG APK************//////////////
///////////////////////////////////////////////////////////

void ReadBT(){
  if(Serial.available() > 0){
    int bt;
    bt=Serial.read();

    /*Movimientos*/
    if(bt=='a'){estado=1;esp=0;}//Alante
    if(bt=='b'){estado=2;esp=0;}//IzquierdaN
    if(bt=='c'){estado=3;esp=0;}//DerechaL
    if(bt=='d'){estado=0;esp=0;}//Stop
    if(bt=='e'){estado=4;esp=0;}//DerechaN
    if(bt=='f'){estado=5;esp=0;}//IzquierdaL
    if(bt=='g'){estado=6;esp=0;}//Atras

    /*Caritas*/
    if(bt=='h'){car=0;}
    if(bt=='i'){car=1;}
    if(bt=='j'){car=2;}
    if(bt=='k'){car=3;}

    /*Ultrasonidos*/
    if(bt=='s'){ut=1;}
    if(bt=='l'){ut=0;}

    /*Otros*/
    if(bt=='o'){esp=1;estado=9;}
    if(bt=='p'){esp=2;estado=9;}
    if(bt=='q'){esp=3;estado=9;}
    if(bt=='r'){esp=4;estado=9;}

    /*Working?*/
    if(bt=='?'){Serial.println("I'm working");}
    
  }
  
}

///////////////////////////////////////////////////////////
//////************FUNCIONES DE MOVIMIENTO************//////
///////////////////////////////////////////////////////////

void Parado(){                       // Parado
  aservo.write(VCA);
  bservo.write(VCB);
  cservo.write(VCC);
  dservo.write(VCD);
}

void Alante(){                       // Alante
  int ang=22;
  aservo.write(VCA+ang);
  bservo.write(VCB);
  cservo.write(VCC);
  dservo.write(VCD+ang);
  delay(vel);
  ReadBT();
  if(estado==0){return;}
  aservo.write(VCA+ang);
  bservo.write(VCB-ang);
  cservo.write(VCC-ang);
  dservo.write(VCD+ang);
  delay(vel);
  ReadBT();
  if(estado==0){return;}
  aservo.write(VCA);
  bservo.write(VCB-ang);
  cservo.write(VCC-ang);
  dservo.write(VCD);
  delay(vel+50);
  ReadBT();
  if(estado==0){return;}
  aservo.write(VCA-ang);
  bservo.write(VCB-ang);
  cservo.write(VCC-ang);
  dservo.write(VCD-ang);
  delay(vel);
  ReadBT();
  if(estado==0){return;}
  aservo.write(VCA+ang);
  bservo.write(VCB-ang);
  cservo.write(VCC-ang);
  dservo.write(VCD+ang);
  delay(vel);
  ReadBT();
  if(estado==0){return;}
  aservo.write(VCA);
  bservo.write(VCB+ang);
  cservo.write(VCC+ang);
  dservo.write(VCD);
  delay(vel+50);
  ReadBT();
  if(estado==0){return;}
  aservo.write(VCA+ang);
  bservo.write(VCB+ang);
  cservo.write(VCC+ang);
  dservo.write(VCD+ang);
  delay(vel+50);
  ReadBT();
  if(estado==0){return;}

  aservo.write(VCA+ang);
  bservo.write(VCB);
  cservo.write(VCC);
  dservo.write(VCD+ang);
  delay(vel);
  ReadBT();
  if(estado==0){return;}
  aservo.write(VCA-ang);
  bservo.write(VCB+ang);
  cservo.write(VCC+ang);
  dservo.write(VCD-ang);
  delay(vel);
  ReadBT();
  if(estado==0){return;}
  aservo.write(VCA);
  bservo.write(VCB+ang);
  cservo.write(VCC+ang);
  dservo.write(VCD);
  delay(vel+50);
  ReadBT();
  if(estado==0){return;}
  aservo.write(VCA+ang);
  bservo.write(VCB+ang);
  cservo.write(VCC+ang);
  dservo.write(VCD+ang);
  delay(vel);
  ReadBT();
  if(estado==0){return;}
  aservo.write(VCA-ang);
  bservo.write(VCB+ang);
  cservo.write(VCC+ang);
  dservo.write(VCD-ang);
  delay(vel);
  ReadBT();
  if(estado==0){return;}
  aservo.write(VCA);
  bservo.write(VCB-ang);
  cservo.write(VCC-ang);
  dservo.write(VCD);
  delay(vel+50);
  ReadBT();
  if(estado==0){return;}
  aservo.write(VCA-ang);
  bservo.write(VCB-ang);
  cservo.write(VCC-ang);
  dservo.write(VCD-ang);
  delay(vel+200);
  ReadBT();
  if(estado==0){return;}
  
}

void Atras(){                        // Atras
  int ang=22;
  aservo.write(VCA+ang);
  bservo.write(VCB);
  cservo.write(VCC);
  dservo.write(VCD+ang);
  delay(vel);
  ReadBT();
  if(estado==0){return;}
  aservo.write(VCA+ang);
  bservo.write(VCB+ang);
  cservo.write(VCC+ang);
  dservo.write(VCD+ang);
  delay(vel);
  ReadBT();
  if(estado==0){return;}
  aservo.write(VCA);
  bservo.write(VCB+ang);
  cservo.write(VCC+ang);
  dservo.write(VCD);
  delay(vel+50);
  ReadBT();
  if(estado==0){return;}
  aservo.write(VCA-ang);
  bservo.write(VCB+ang);
  cservo.write(VCC+ang);
  dservo.write(VCD-ang);
  delay(vel);
  ReadBT();
  if(estado==0){return;}
  aservo.write(VCA+ang);
  bservo.write(VCB+ang);
  cservo.write(VCC+ang);
  dservo.write(VCD+ang);
  delay(vel);
  ReadBT();
  if(estado==0){return;}
  aservo.write(VCA);
  bservo.write(VCB-ang);
  cservo.write(VCC-ang);
  dservo.write(VCD);
  delay(vel+50);
  ReadBT();
  if(estado==0){return;}
  aservo.write(VCA+ang);
  bservo.write(VCB-ang);
  cservo.write(VCC-ang);
  dservo.write(VCD+ang);
  delay(vel+50);
  ReadBT();
  if(estado==0){return;}

  aservo.write(VCA+ang);
  bservo.write(VCB);
  cservo.write(VCC);
  dservo.write(VCD+ang);
  delay(vel);
  ReadBT();
  if(estado==0){return;}
  aservo.write(VCA-ang);
  bservo.write(VCB-ang);
  cservo.write(VCC-ang);
  dservo.write(VCD-ang);
  delay(vel);
  ReadBT();
  if(estado==0){return;}
  aservo.write(VCA);
  bservo.write(VCB-ang);
  cservo.write(VCC-ang);
  dservo.write(VCD);
  delay(vel+50);
  ReadBT();
  if(estado==0){return;}
  aservo.write(VCA+ang);
  bservo.write(VCB-ang);
  cservo.write(VCC-ang);
  dservo.write(VCD+ang);
  delay(vel);
  ReadBT();
  if(estado==0){return;}
  aservo.write(VCA-ang);
  bservo.write(VCB-ang);
  cservo.write(VCC-ang);
  dservo.write(VCD-ang);
  delay(vel);
  ReadBT();
  if(estado==0){return;}
  aservo.write(VCA);
  bservo.write(VCB+ang);
  cservo.write(VCC+ang);
  dservo.write(VCD);
  delay(vel+50);
  ReadBT();
  if(estado==0){return;}
  aservo.write(VCA-ang);
  bservo.write(VCB+ang);
  cservo.write(VCC+ang);
  dservo.write(VCD-ang);
  delay(vel+200);
  ReadBT();
  if(estado==0){return;}
}

void Derechal(){                     // Derecha lateral
  int ang=30;
  aservo.write(VCA-ang);
  bservo.write(VCB);
  cservo.write(VCC);
  dservo.write(VCD+ang);
  delay(vel);
  aservo.write(VCA-ang);
  bservo.write(VCB);
  cservo.write(VCC);
  dservo.write(VCD);
  delay(vel);
  aservo.write(VCA);
  bservo.write(VCB);
  cservo.write(VCC);
  dservo.write(VCD);
  delay(vel);
}

void Izquierdal(){                   // Izquierda Lateral
  int ang=30;
  aservo.write(VCA-ang);
  bservo.write(VCB);
  cservo.write(VCC);
  dservo.write(VCD+ang);
  delay(vel);
  aservo.write(VCA);
  bservo.write(VCB);
  cservo.write(VCC);
  dservo.write(VCD+ang);
  delay(vel);
  aservo.write(VCA);
  bservo.write(VCB);
  cservo.write(VCC);
  dservo.write(VCD);
  delay(vel);
}

void Izquierdan(){                   // Izquierda Normal
  int ang=30;
  aservo.write(VCA+ang);
  bservo.write(VCB);
  cservo.write(VCC);
  dservo.write(VCD+ang);
  delay(vel);
  ReadBT();
  if(estado==0){return;}
  aservo.write(VCA+ang);
  bservo.write(VCB-ang);
  cservo.write(VCC);
  dservo.write(VCD+ang);
  delay(vel);
  ReadBT();
  if(estado==0){return;}
  aservo.write(VCA);
  bservo.write(VCB-ang);
  cservo.write(VCC);
  dservo.write(VCD);
  delay(vel);
  ReadBT();
  if(estado==0){return;}
  aservo.write(VCA-ang);
  bservo.write(VCB-ang);
  cservo.write(VCC);
  dservo.write(VCD-ang);
  delay(vel);
  ReadBT();
  if(estado==0){return;}
  aservo.write(VCA-ang);
  bservo.write(VCB);
  cservo.write(VCC);
  dservo.write(VCD-ang);
  delay(vel);
  ReadBT();
  if(estado==0){return;}
  aservo.write(VCA);
  bservo.write(VCB);
  cservo.write(VCC);
  dservo.write(VCD);
  delay(vel);
  ReadBT();
  if(estado==0){return;}
}

void Derechan(){                   // Derecha Normal
  vel=1000;
  int ang=30;
  aservo.write(VCA-ang);
  bservo.write(VCB);
  cservo.write(VCC);
  dservo.write(VCD-ang);
  delay(vel);
  ReadBT();
  if(estado==0){return;}
  aservo.write(VCA-ang);
  bservo.write(VCB);
  cservo.write(VCC+ang);
  dservo.write(VCD);
  delay(vel);
  ReadBT();
  if(estado==0){return;}
  aservo.write(VCA);
  bservo.write(VCB);
  cservo.write(VCC+ang);
  dservo.write(VCD);
  delay(vel);
  ReadBT();
  if(estado==0){return;}
  aservo.write(VCA+ang);
  bservo.write(VCB);
  cservo.write(VCC+ang);
  dservo.write(VCD+ang);
  delay(vel);
  ReadBT();
  if(estado==0){return;}
  aservo.write(VCA+ang);
  bservo.write(VCB);
  cservo.write(VCC);
  dservo.write(VCD+ang);
  delay(vel);
  ReadBT();
  if(estado==0){return;}
  aservo.write(VCA);
  bservo.write(VCB);
  cservo.write(VCC);
  dservo.write(VCD);
  delay(vel);
  ReadBT();
  if(estado==0){return;}
}

void GirarIzquierda(){                // Giro Izquierda
  int ang=30;
  aservo.write(VCA-ang);
  bservo.write(VCB);
  cservo.write(VCC);
  dservo.write(VCD-ang);
  delay(vel);
  ReadBT();
  if(estado==0){return;}
  aservo.write(VCA-ang);
  bservo.write(VCB);
  cservo.write(VCC+ang);
  dservo.write(VCD-ang);
  delay(vel);
  ReadBT();
  if(estado==0){return;}
  aservo.write(VCA);
  bservo.write(VCB);
  cservo.write(VCC+ang);
  dservo.write(VCD);
  delay(vel);
  ReadBT();
  if(estado==0){return;}
  aservo.write(VCA+ang);
  bservo.write(VCB);
  cservo.write(VCC+ang);
  dservo.write(VCD+ang);
  delay(vel);
  ReadBT();
  if(estado==0){return;}
  aservo.write(VCA+ang);
  bservo.write(VCB);
  cservo.write(VCC);
  dservo.write(VCD+ang);
  delay(vel);
  ReadBT();
  if(estado==0){return;}
  aservo.write(VCA);
  bservo.write(VCB);
  cservo.write(VCC);
  dservo.write(VCD);
  delay(vel);
  ReadBT();
  if(estado==0){return;}
}

void Derechant(){                     // Derecha Normal Trasera
  int ang=20;
  aservo.write(VCA+ang);
  bservo.write(VCB);
  cservo.write(VCC);
  dservo.write(VCD+ang);
  delay(vel);
  ReadBT();
  if(estado==0){return;}
  aservo.write(VCA+ang);
  bservo.write(VCB);
  cservo.write(VCC-ang);
  dservo.write(VCD+ang);
  delay(vel);
  ReadBT();
  if(estado==0){return;}
  aservo.write(VCA);
  bservo.write(VCB);
  cservo.write(VCC-ang);
  dservo.write(VCD);
  delay(vel);
  ReadBT();
  if(estado==0){return;}
  aservo.write(VCA-ang);
  bservo.write(VCB);
  cservo.write(VCC-ang);
  dservo.write(VCD-ang);
  delay(vel);
  ReadBT();
  if(estado==0){return;}
  aservo.write(VCA-ang);
  bservo.write(VCB);
  cservo.write(VCC);
  dservo.write(VCD-ang);
  delay(vel);
  ReadBT();
  if(estado==0){return;}
  aservo.write(VCA);
  bservo.write(VCB);
  cservo.write(VCC);
  dservo.write(VCD);
  delay(vel);
  ReadBT();
  if(estado==0){return;}
}

void IzquierdaNormalTrasera(){
  int ang=30;
  aservo.write(VCA-ang);
  bservo.write(VCB);
  cservo.write(VCC);
  dservo.write(VCD-ang);
  delay(vel);
  ReadBT();
  if(estado==0){return;}
  aservo.write(VCA-ang);
  bservo.write(VCB);
  cservo.write(VCC-ang);
  dservo.write(VCD-ang);
  delay(vel);
  ReadBT();
  if(estado==0){return;}
  aservo.write(VCA);
  bservo.write(VCB);
  cservo.write(VCC-ang);
  dservo.write(VCD);
  delay(vel);
  ReadBT();
  if(estado==0){return;}
  aservo.write(VCA+ang);
  bservo.write(VCB);
  cservo.write(VCC-ang);
  dservo.write(VCD+ang);
  delay(vel);
  ReadBT();
  if(estado==0){return;}
  aservo.write(VCA+ang);
  bservo.write(VCB);
  cservo.write(VCC);
  dservo.write(VCD+ang);
  delay(vel);
  ReadBT();
  if(estado==0){return;}
  aservo.write(VCA);
  bservo.write(VCB);
  cservo.write(VCC);
  dservo.write(VCD);
  delay(vel);
  ReadBT();
  if(estado==0){return;}
}

void Moverservosbcconpausa(){        // Mover ByC
  int ang=50;
  bservo.write(VCB+ang);
  cservo.write(VCC+ang);
  delay(vel);
  bservo.write(VCB+ang);
  cservo.write(VCC+ang);
  delay(vel*2);
  bservo.write(VCB);
  cservo.write(VCC);
  delay(vel*2);
  bservo.write(VCB-ang);
  cservo.write(VCC-ang);
  delay(vel);
  bservo.write(VCB-ang);
  cservo.write(VCC-ang);
  delay(vel*2);
  bservo.write(VCB);
  cservo.write(VCC);
  delay(vel*2);
}

void Moverservosbcsinpausa(){        // Mover ByC
  int ang=50;
  bservo.write(VCB+ang);
  cservo.write(VCC+ang);
  delay(vel);
  bservo.write(VCB+ang);
  cservo.write(VCC+ang);
  delay(vel*2);
  bservo.write(VCB-ang);
  cservo.write(VCC-ang);
  delay(vel);
  bservo.write(VCB-ang);
  cservo.write(VCC-ang);
  delay(vel*2);
  bservo.write(VCB-ang);
  cservo.write(VCC-ang);
  delay(vel);
  bservo.write(VCB-ang);
  cservo.write(VCC-ang);
  delay(vel*2);
  bservo.write(VCB+ang);
  cservo.write(VCC+ang);
  delay(vel);
  bservo.write(VCB+ang);
  cservo.write(VCC+ang);
  delay(vel*2);
}

void Ponerpuntillas(){               // Poner de puntillas
  int cont=0;
  for(cont>0;cont<70;cont++){
    aservo.write(VCA-cont);
    bservo.write(VCB);
    cservo.write(VCC);
    dservo.write(VCD+cont);
    delay(5);  
  }
}
void Quitarpuntillas(){              // Quitar de puntillas
  int cont=70;
  for(cont<70;cont>0;cont--){
    aservo.write(VCA-cont);
    bservo.write(VCB);
    cservo.write(VCC);
    dservo.write(VCD+cont);
    delay(5);  
  }  
}

void Asustar(){                      // Asustar
   aservo.write(VCA+70);
   bservo.write(VCB);
   cservo.write(VCC);
   dservo.write(VCD-70);
   delay(200);
   aservo.write(VCA+70);
   bservo.write(VCB-40);
   cservo.write(VCC+40);
   dservo.write(VCD-70);
   delay(100);
}

void Desasustar(){                   // Desasustar
   aservo.write(VCA+70);
   bservo.write(VCB);
   cservo.write(VCC);
   dservo.write(VCD-70);
   delay(100);
   aservo.write(VCA);
   bservo.write(VCB);
   cservo.write(VCC);
   dservo.write(VCD);
   delay(100);
}

void Saludo(){                       // Saludo
  int ang=32;
  aservo.write(VCA+ang-10);
  bservo.write(VCB);
  cservo.write(VCC);
  dservo.write(VCD+90);
  delay(100);
  aservo.write(VCA+ang);
  bservo.write(VCB);
  cservo.write(VCC);
  dservo.write(VCD+90);
  delay(400);
  aservo.write(VCA+ang);
  bservo.write(VCB);
  cservo.write(VCC);
  dservo.write(VCD-40);
  delay(400);
  aservo.write(VCA+ang);
  bservo.write(VCB);
  cservo.write(VCC);
  dservo.write(VCD+40);
  delay(400);
  aservo.write(VCA+ang);
  bservo.write(VCB);
  cservo.write(VCC);
  dservo.write(VCD-40);
  delay(400);
  aservo.write(VCA+ang);
  bservo.write(VCB);
  cservo.write(VCC);
  dservo.write(VCD+40);
  delay(400);
  aservo.write(VCA+ang);
  bservo.write(VCB);
  cservo.write(VCC);
  dservo.write(VCD-40);
  delay(400);
  aservo.write(VCA+ang);
  bservo.write(VCB);
  cservo.write(VCC);
  dservo.write(VCD+40);
  delay(400);
  aservo.write(VCA+ang);
  bservo.write(VCB);
  cservo.write(VCC);
  dservo.write(VCD-40);
  delay(400);
  aservo.write(VCA);
  bservo.write(VCB);
  cservo.write(VCC);
  dservo.write(VCD);
  delay(200);
}

void Servoread(){                    // Lectura de servos
  Serial.print("ServoA=");
  Serial.print(aservo.read());
  Serial.print(" ServoB=");
  Serial.print(bservo.read());
  Serial.print(" ServoC=");
  Serial.print(cservo.read());
  Serial.print(" ServoD=");
  Serial.println(dservo.read());
  delay(10);
}


///////////////////////////////////////////////////////////
///////////////************Baile************///////////////
///////////////////////////////////////////////////////////
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

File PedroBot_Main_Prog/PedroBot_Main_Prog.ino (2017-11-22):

//----------------------------------------------------------------
//-- Zowi basic firmware v2.1 for battery support
//-- (c) BQ. Released under a GPL licencse
//-- 04 December 2015
//-- Authors:  Anita de Prado: ana.deprado@bq.com
//--           Jose Alberca:   jose.alberca@bq.com
//--           Javier Isabel:  javier.isabel@bq.com
//--           Juan Gonzalez (obijuan): juan.gonzalez@bq.com
//--           Irene Sanz : irene.sanz@bq.com
//-----------------------------------------------------------------
//-- Experiment with all the features that Zowi have!
//-----------------------------------------------------------------

#include <Servo.h>
#include <Oscillator.h>
#include <EEPROM.h>
#include <BatReader.h>
#include <US.h>
#include <LedMatrix.h>

//-- Library to manage external interruptions
#include <EnableInterrupt.h>

//-- Library to manage serial commands
#include <ZowiSerialCommand.h>
ZowiSerialCommand SCmd;  //The SerialCommand object

//-- Zowi Library
#include <Zowi.h>
Zowi zowi;  //This is Zowi!!

//---------------------------------------------------------
//-- Configuration of pins where the servos are attached
/*
         ---------------
        |               |
        |     O   O     |
        |               |
 YR ==> |               | <== YL
         ---------------
            ||     ||
            ||     ||
            ||     ||
 RR ==>   -----   ------  <== RL
          -----   ------
*/

#define PIN_YL 2 //servo[0]
#define PIN_YR 3 //servo[1]
#define PIN_RL 4 //servo[2]
#define PIN_RR 5 //servo[3]

//---------------------------------------------------------

///////////////////////////////////////////////////////////////////
//-- Global Variables -------------------------------------------//
///////////////////////////////////////////////////////////////////

const char programID[] = "ZOWI_BASE_v2"; //Each program will have a ID

const char name_fac = '$'; //Factory name
const char name_fir = '#'; //First name

//-- Movement parameters
int T = 1000;            //Initial duration of movement
int moveId = 0;          //Number of movement
int moveSize = 15;       //Asociated with the height of some movements

//---------------------------------------------------------
//-- Zowi has 5 modes:
//--    * MODE = 0: Zowi is awaiting
//--    * MODE = 1: Dancing mode!
//--    * MODE = 2: Obstacle detector mode
//--    * MODE = 3: Noise detector mode
//--    * MODE = 4: ZowiPAD or any Teleoperation mode (listening SerialPort).
//--
volatile int MODE = 0; //State of zowi in the principal state machine.
//---------------------------------------------------------

volatile bool buttonPushed = false; //Variable to remember when a button has been pushed
volatile bool buttonAPushed = false; //Variable to remember when A button has been pushed
volatile bool buttonBPushed = false; //Variable to remember when B button has been pushed

unsigned long previousMillis = 0;

int randomDance = 0;
int randomSteps = 0;

bool obstacleDetected = false;

//--------------------------------------------------------------------------
// Pedro-51 variables

int usb_connect = A1;
int usb_val = 0;
volatile bool start = true;

///////////////////////////////////////////////////////////////////
//-- Setup ------------------------------------------------------//
///////////////////////////////////////////////////////////////////
void setup() {

  //Serial communication initialization
  Serial.begin(115200);

  //---Zowi Buttons
  #define PIN_AButton 6
  #define PIN_BButton 7

  pinMode(PIN_AButton, INPUT);
  pinMode(PIN_BButton, INPUT);
  pinMode(usb_connect, INPUT);

  //Set the servo pins
  zowi.init(PIN_YL, PIN_YR, PIN_RL, PIN_RR, true);

  //Zowi wake up!
  zowi.home();

  //Uncomment this to set the servo trims manually and save on EEPROM
  //zowi.setTrims(TRIM_YL, TRIM_YR, TRIM_RL, TRIM_RR);
  //zowi.saveTrimsOnEEPROM(); //Uncomment this only one upload when you finaly set the trims.

  //Set a random seed
  randomSeed(analogRead(A6));

  //Interrumptions
  enableInterrupt(PIN_AButton, AButtonPushed, RISING);
  enableInterrupt(PIN_BButton, BButtonPushed, RISING);

  //Setup callbacks for SerialCommand commands
  SCmd.addCommand("S", receiveStop);      //  sendAck & sendFinalAck
  SCmd.addCommand("L", receiveLED);       //  sendAck & sendFinalAck
  SCmd.addCommand("T", recieveBuzzer);    //  sendAck & sendFinalAck
  SCmd.addCommand("M", receiveMovement);  //  sendAck & sendFinalAck
  SCmd.addCommand("H", receiveGesture);   //  sendAck & sendFinalAck
  SCmd.addCommand("K", receiveSing);      //  sendAck & sendFinalAck
  SCmd.addCommand("C", receiveTrims);     //  sendAck & sendFinalAck
  SCmd.addCommand("G", receiveServo);     //  sendAck & sendFinalAck
  SCmd.addCommand("R", receiveName);      //  sendAck & sendFinalAck
  SCmd.addCommand("E", requestName);
  SCmd.addCommand("D", requestDistance);
  SCmd.addCommand("N", requestNoise);
  SCmd.addCommand("B", requestBattery);
  SCmd.addCommand("I", requestProgramId);
  SCmd.addDefaultHandler(receiveStop);

  //If Zowi's name is '&' (factory name) means that is the first time this program is executed.
  //This first time, Zowi mustn't do anything. Just born at the factory!
  //5 = EEPROM address that contains first name character
  if (EEPROM.read(5) == name_fac) {

    EEPROM.put(5, name_fir); //From now, the name is '#'
    EEPROM.put(6, '\0');
    zowi.putMouth(culito);

    while (true) {
      delay(1000);
    }
  }

  //Checking usb connect
  usb_val = digitalRead(usb_connect);
  if (usb_val == true) {
    Charging();
  }
  //Desactive start value
  start = false;

  //Send Zowi name, programID & battery level.
  requestName();
  delay(50);
  requestProgramId();
  delay(50);
  requestBattery();

  //Checking battery
  ZowiLowBatteryAlarm();

  // Animation Uuuuuh - A little moment of initial surprise
  //-----
   /*   for (int i=0;i<16;i++){
        if(buttonPushed){break;}  
        zowi.putAnimationMouth(littleUuh,i);
        delay(100);
      } */
  //-----

  //Smile for a happy Zowi :)
  if (!buttonPushed) {
    zowi.putMouth(smile);
    zowi.sing(S_happy);
    delay(200);
  }

  //If Zowi's name is '#' means that Zowi hasn't been baptized
  //In this case, Zowi does a longer greeting
  //5 = EEPROM address that contains first name character
  if (EEPROM.read(5) == name_fir) {

    if (!buttonPushed) {
      zowi.jump(1, 700);
      delay(200);
    }

    if (!buttonPushed) {
      zowi.shakeLeg(1, T, 1);
    }

    if (!buttonPushed) {
      zowi.putMouth(smallSurprise);
      zowi.swing(2, 800, 20);
      zowi.home();
    }
  }

  if (!buttonPushed) {
    zowi.putMouth(happyOpen);
  }

  previousMillis = millis();

}
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

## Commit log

2017-07-11 Otto DIY+
    Optimized libraries for less memory use, added RGB led, LedMatrix, BT, version with buttons or touch sensor.
2017-09-04 Added alarm mode
    Works with touch sensor and buttons, firs button is mode + and second button is mode -, added alarm and guardian modes from Zowi.
2017-09-07 Nose detection corretion
    Changed noise sensing so it should be more accurate now, buffer in maxmatrix.h is 5 now and added modee six, which just shows random number from 0-9.
    [Otto_v3.ino]
2017-11-22 codes to test
    please help me to try these codes in Otto
    [Corps v1.4.stl, Corps v1.5 MG.stl, Corps.FCStd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]
2017-11-23 matrix STL
    files so you can fit Matrix and AA batteries
    [Body_MATRIX_4.stl, Head_MATRIX_5.stl]
2017-12-12 measure battery level
2018-02-01 biped builds
    collection of family members of Otto
    need unify libraries, codes and boards
